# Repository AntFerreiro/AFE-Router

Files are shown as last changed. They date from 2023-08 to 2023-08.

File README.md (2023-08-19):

# AFE Router Documentation
This repository contain all materials for the assembly of the second version of this CNC Machine. 

This documentation is free and any commercial use is not allowed. Make sure to follow the repository to get the latest updates.

I hope you enjoy the project!

## Software
This machine is based on Marlin for the firmware. An extra branch has been created for this machine [AFE Router Version 2.0](https://github.com/AntFerreiro/Marlin)
For extra support and documentation for the firmware, go check the official [Marlin](https://github.com/MarlinFirmware/Marlin) repository.

## Drawings
Drawings are provided since not everyone may use the STL files as they are. Drawings make possible to modify some pieces so the still match with the rest of the machine.

## STL Files
STL files can be downloaded from this repository and can also be found in [Thingiverse](https://www.thingiverse.com/aferreiro_21/designs)
There is also the first version of this machine as well as some other designs I made.

## CNC Programs
You can also have a look at some of the CNC programms I use in the dayly work. This CNC programs are already tested in my machine but they may need some modifications if your machine is different (workspace limits for example).

## Bill of materials
The Hardware I used for this machine will be listed as well as the price I paid for them. This may vary with time depending on some temporary offers.

## Assembly instructions
There is no assembly manual that you can follow step by step. However here is the video I made when I built my machines. Since this is a progressive project. Not every step may be filmed in the video so make sure to subscribe to get the latest modifications.

Watch full video (https://www.youtube.com/watch?v=1IjvXwbKiRI)

## Do you want to support?
I'm not selling anything so if you want to support me, you can follow me on [social media](https://www.instagram.com/truewoodpecker/) and visit my [YouTube](https://www.youtube.com/@antonioferreiro) channel to give a big like and subscribe!

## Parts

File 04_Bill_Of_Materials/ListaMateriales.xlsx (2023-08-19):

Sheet: Hardware
 |  |  | Total Cost | 423.82
Item | Qty | Specs | Desctription | Price
Screw Bar | 3 | Pitch 2mm Lead 8mm, 100mm |  | 3.31 | https://es.aliexpress.com/item/1005004337655460.html
 | 1 | Pitch 2mm Lead 8mm, 600mm |  | 10.5
 | 2 | Pitch 2mm Lead 8mm, 400mm |  | 5.3
 | 1 | Pitch 2mm Lead 8mm, 250mm |  | 4
PowerSupply | 1 | 48V |  | 28.5 | https://es.aliexpress.com/item/1005002728038351.html
 | 1 | 12V |  | 8.21 | https://www.banggood.com/de/Geekcreit-AC-100-240V-to-DC-12V-5A-60W-Switching-Power-Supply-Module-Driver-Adapter-LED-Strip-Light-p-1441620.html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
Spindle | 1 | 400W | ER11 | 45.8 | https://es.aliexpress.com/item/32927775609.html
Nuts | 1 | M5 |  | 13.95 | https://es.aliexpress.com/item/32966882545.html
 | 1 | M3 |  | 15
Linear Bearing | 2 | MGN15H, 400mm |  | 22 | https://es.aliexpress.com/item/4000264234020.html
 | 2 | MGN15H, 600mm |  | 31.63
 | 2 | MGN9C |  | 7.32
 | 2 | MGN9C, 200mm |  | 11.31
Aluminium Profile | 2 | 2080, 400MM |  | 15.095 | https://es.aliexpress.com/item/1005002645411058.html
 | 2 | 2020, 500MM |  | 7.625
 | 2 | 2080, 500MM |  | 18.29
 | 1 | 2080, 600mm |  | 23.85 | https://es.aliexpress.com/item/1005004324352655.html
Pulley | 1 | 20-30T W6 B5 |  | 1.5 | https://es.aliexpress.com/item/1005005247772974.html
Ramps 1.6 | 1 | 1.6 |  | 5 | https://es.aliexpress.com/item/1005005074906263.html?curPageLogUid=tiiyxxNTx6R9
Stepper Drivers | 4 | A4988 |  | 0.86 | https://es.aliexpress.com/item/1005001621676770.html?curPageLogUid=2uASGiAAFuzh
Arduino Mega | 1 |  |  | 17 | https://es.aliexpress.com/item/32513419382.html?curPageLogUid=S8TSfbzLelJ8

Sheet: Screws
 | INCOMPLETO!
tornilleria |  | cantidad | metrica | mm | mm alt | coment
 | display | 4 | M3 | 10
 | Estop | 2 | M3 | 10
 | Motor eje Y | 8 | M5 | 12 | 10
 |  | 8 | M3 | 12 |  | \_/
 |  | 2 | M3 | 5
 | Guias Y | 20 | M3 | 10
 | Base | 20 | M5 | 10
 |  | 16 | M3 | 5 | 8 | \_/
 |  | 48 | M5 | 10
 | Lateral eje X | 8 | M3 | 15
 |  | 16 | M3 | 20
 |  | 8 | M3 | 26 | 30
 |  | 8 | M5 | 30
 |  | 4 | M3 | 32 | 35
 | Guias x | 30 | M3 | 10
 | Perfil L | 2 | M3 | 11 | 15
 | Guias Z | 18 | M3 | 10 | 12
 | soporte rodamiento | 2 | M4 | 75

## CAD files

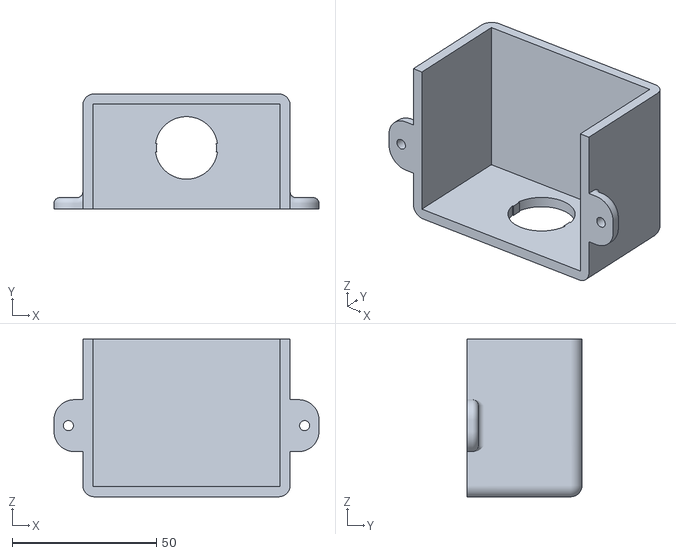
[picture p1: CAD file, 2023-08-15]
02_STL files/01_Base/EStop_Cover.stl
92.0 x 40.0 x 54.7

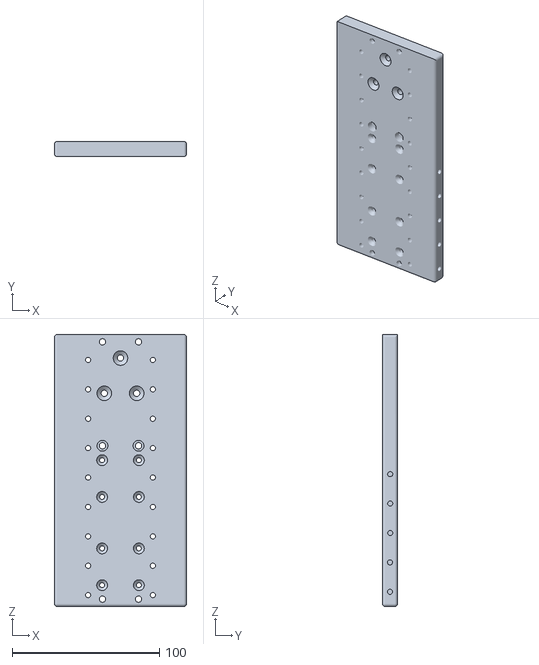
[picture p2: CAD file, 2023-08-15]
02_STL files/02_X_carriage/Carro_eje_X_plate.stl
90.0 x 10.3 x 185.0

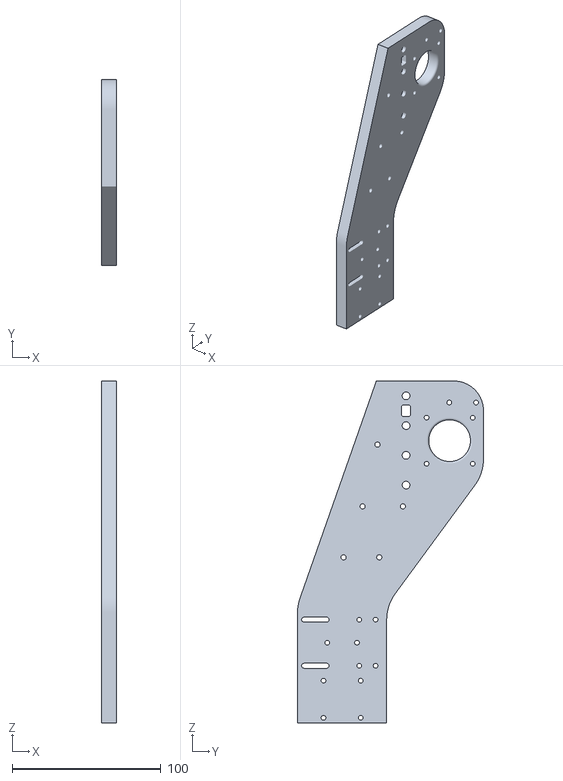
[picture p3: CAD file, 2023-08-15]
02_STL files/03_Y_carriage/Carro_eje_Y_plate_mot.stl
10.0 x 125.1 x 230.0

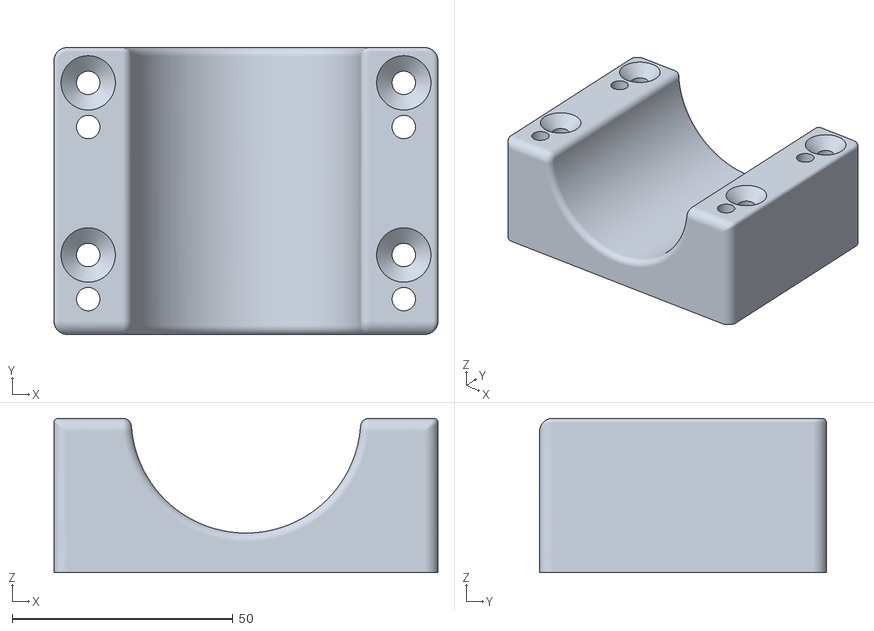
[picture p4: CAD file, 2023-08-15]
02_STL files/04_Z_carriage/spindle_holder_53mm.stl
87.0 x 65.0 x 35.0

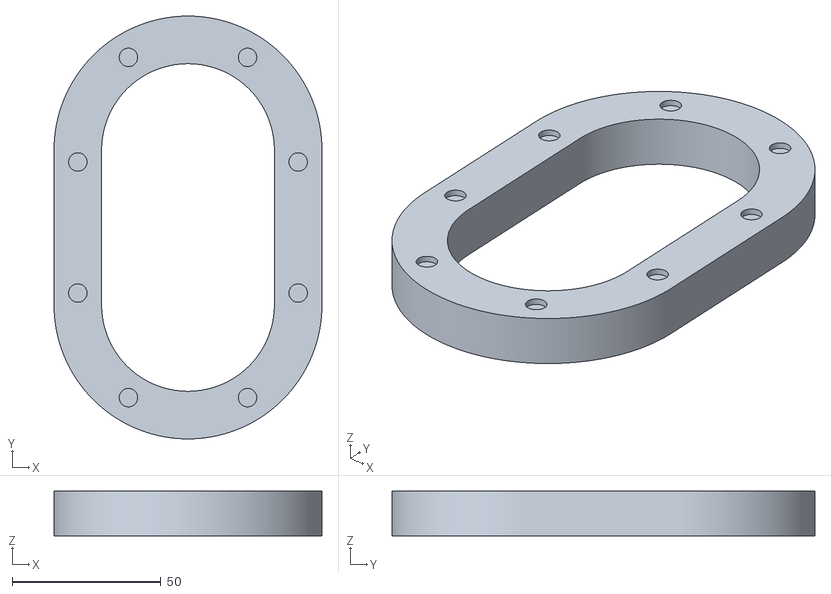
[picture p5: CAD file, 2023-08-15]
02_STL files/05_Vacuum/Foam_holder.stl
90.0 x 142.0 x 15.0

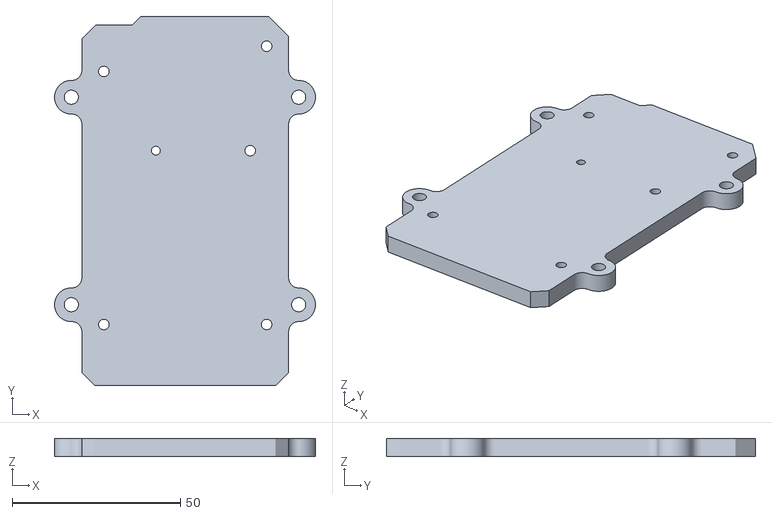
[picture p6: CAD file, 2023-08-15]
02_STL files/01_Base/ramps_1.6_holder.stl
77.5 x 109.6 x 5.45

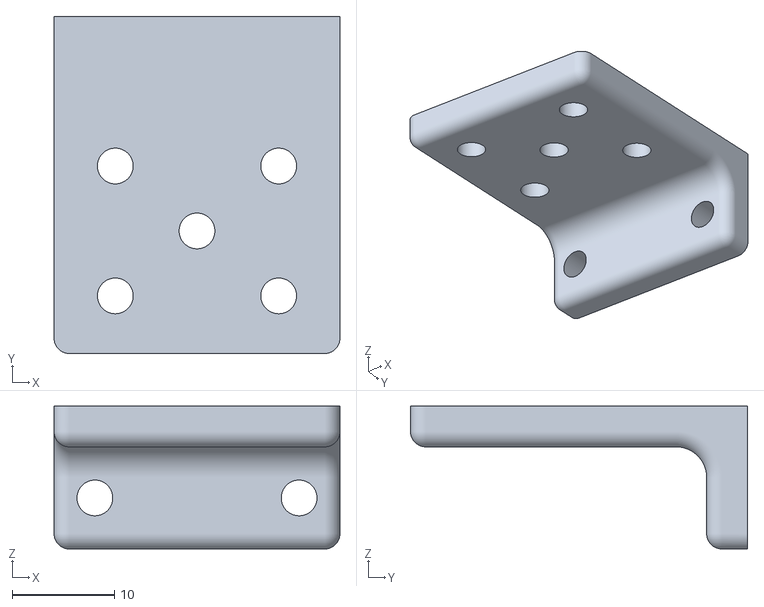
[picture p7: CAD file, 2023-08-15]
02_STL files/03_Y_carriage/CableChain_holder.stl
28.0 x 33.0 x 14.0

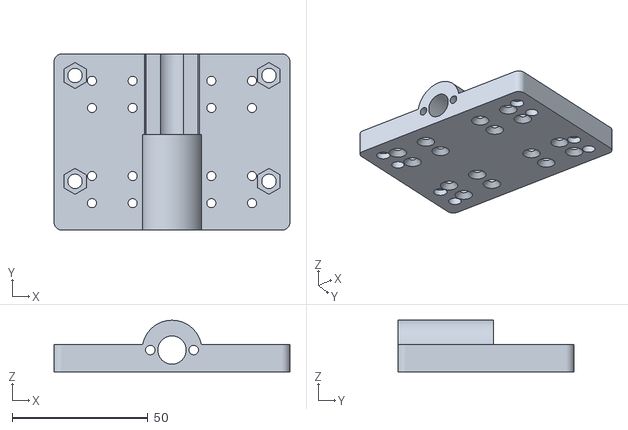
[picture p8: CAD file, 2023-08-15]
02_STL files/04_Z_carriage/Carro_eje_Z_platev2.stl
87.0 x 65.0 x 19.0

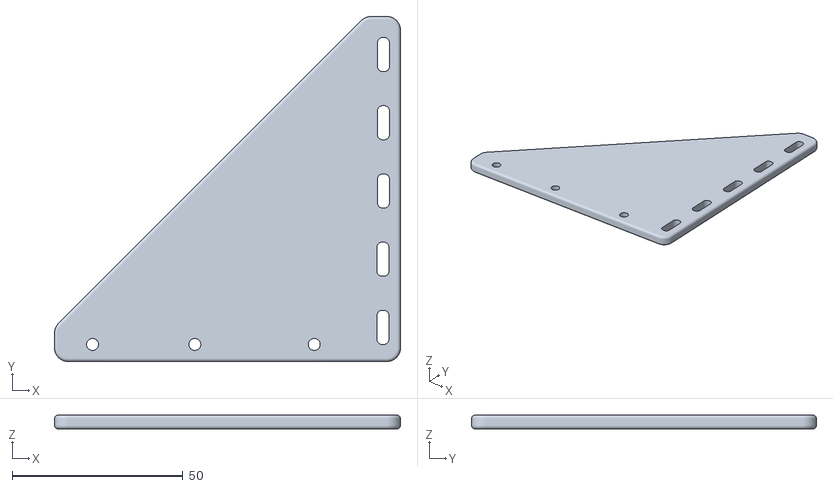
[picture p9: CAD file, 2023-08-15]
02_STL files/05_Vacuum/Vacuum_holder2.stl
101.5 x 101.2 x 4.00

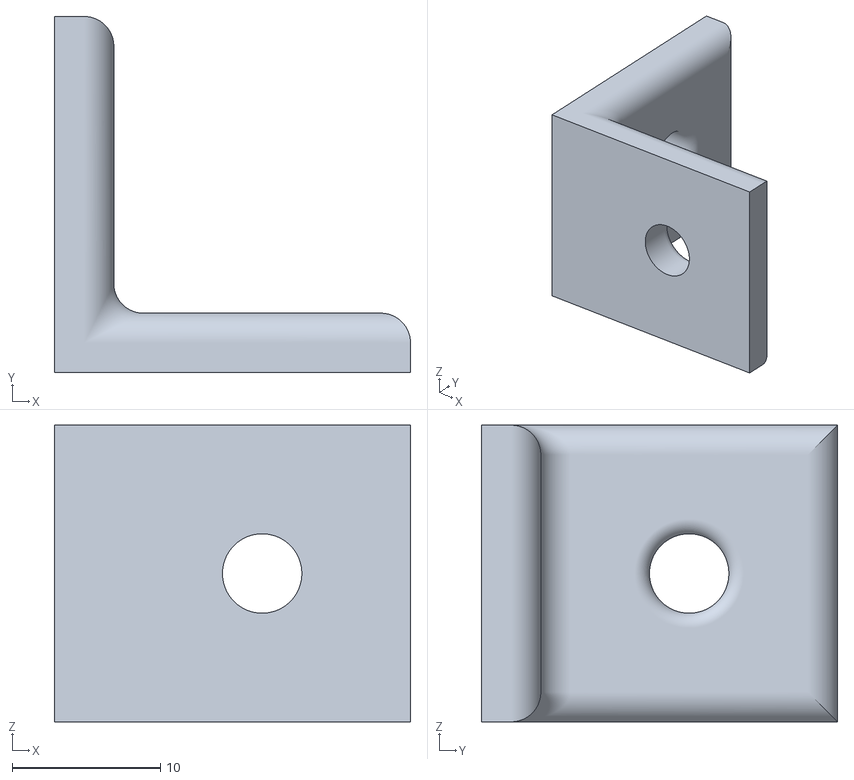
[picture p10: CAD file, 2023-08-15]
02_STL files/01_Base/Fixment.stl
24.0 x 24.0 x 20.0

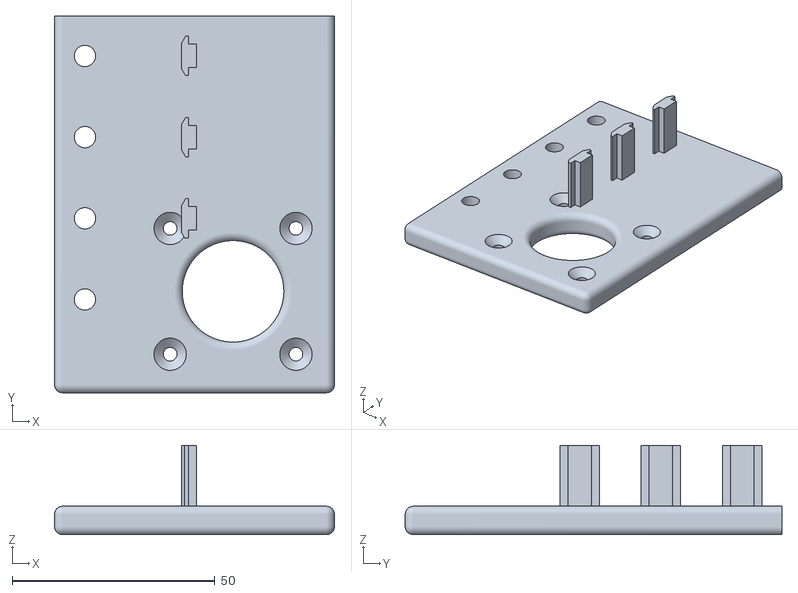
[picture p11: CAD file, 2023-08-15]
02_STL files/01_Base/Motor_Cover_2.stl
69.0 x 92.8 x 22.0

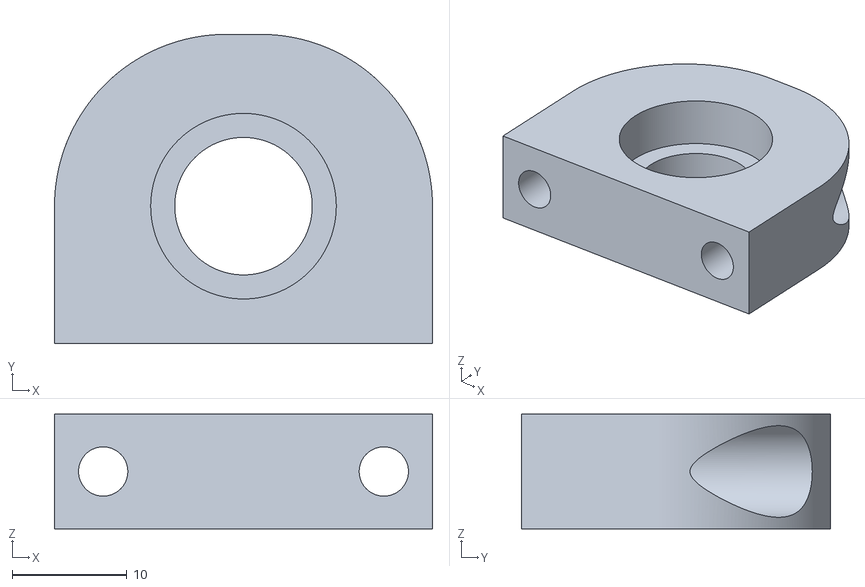
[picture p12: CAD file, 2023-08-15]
02_STL files/02_X_carriage/bearing_holder2_conic.stl
33.0 x 27.0 x 10.0

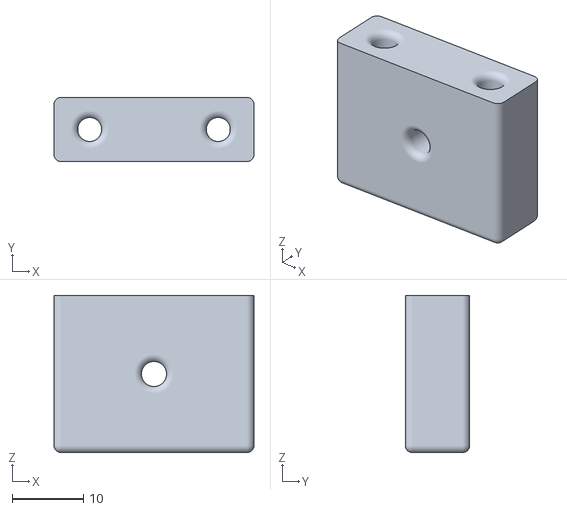
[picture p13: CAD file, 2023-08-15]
02_STL files/03_Y_carriage/Profile_holder.stl
28.0 x 9.00 x 22.0

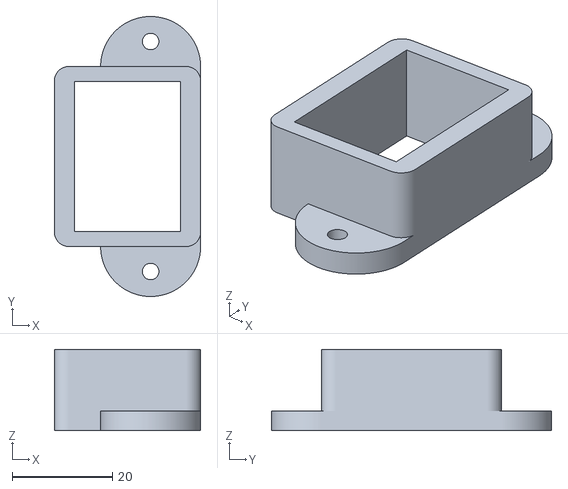
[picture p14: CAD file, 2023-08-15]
02_STL files/01_Base/Switch_holder.stl
29.2 x 56.0 x 16.3

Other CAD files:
02_STL files/02_X_carriage/Carro_eje_X_plate_back.stl
02_STL files/03_Y_carriage/Carro_eje_Y_plate.stl
02_STL files/01_Base/AC_DC_12V_support.stl
02_STL files/01_Base/Fan_Holder.stl
02_STL files/01_Base/AC_holder.stl
02_STL files/01_Base/Fixment20x20.stl
02_STL files/01_Base/Relay_holder.stl
02_STL files/01_Base/Top_Display.stl
02_STL files/01_Base/USB_holder.stl
02_STL files/01_Base/bearing_holder.stl
02_STL files/02_X_carriage/Carro_eje_X_plate_bottom.stl
02_STL files/02_X_carriage/Carro_eje_X_plate_top1.stl
02_STL files/02_X_carriage/LSHolder_v3.stl
02_STL files/02_X_carriage/LeadScrew_Block2.stl
02_STL files/02_X_carriage/LeadScrew_Block3.stl
02_STL files/02_X_carriage/bearing_holder2.stl
02_STL files/02_X_carriage/bearing_holder2Vscrew.stl
02_STL files/02_X_carriage/bearing_holder2_flat.stl
02_STL files/03_Y_carriage/LeadScrew_Block1.stl

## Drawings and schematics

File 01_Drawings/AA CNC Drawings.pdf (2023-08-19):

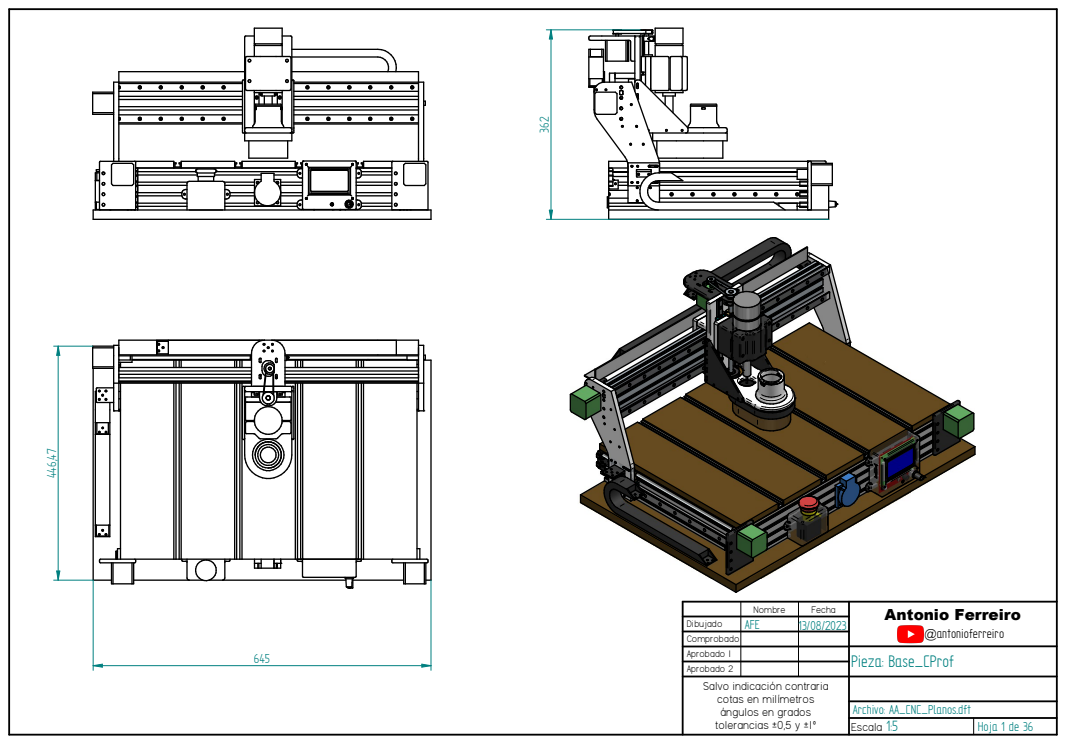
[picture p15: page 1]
Archivo: AA_CNC_Planos.dft

Nombre | Fecha | Antonio Ferreiro @antonioferreiro

Dibujado | AFE | 13/08/2023
Comprobado
Aprobado 1 | | | Pieza: Base_CProf
Aprobado 2
Salvo indicación contraria cotas en milímetros ángulos en grados tolerancias ±0,5 y ±1º

Escala 1:5 | Hoja 1 de 36

Nombre | Fecha | Antonio Ferreiro @antonioferreiro

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

Escala 1:5 | Hoja 2 de 36

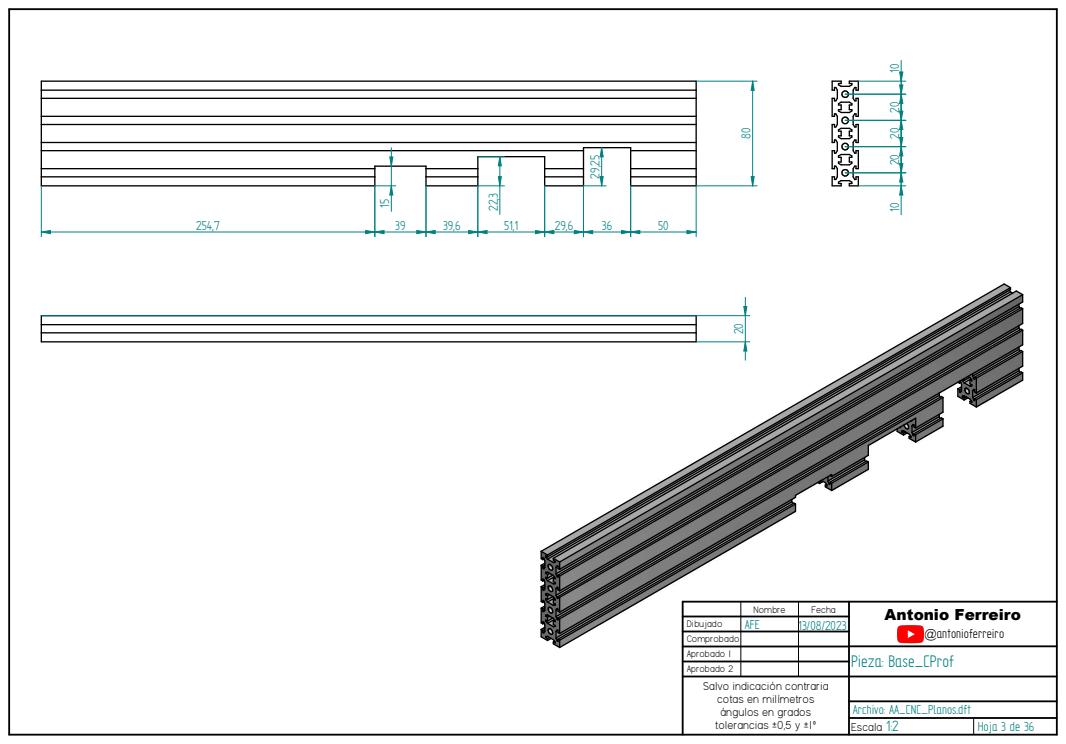
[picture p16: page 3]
Archivo: AA_CNC_Planos.dft

Nombre | Fecha | Antonio Ferreiro @antonioferreiro

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

Escala 1:2 | Hoja 3 de 36

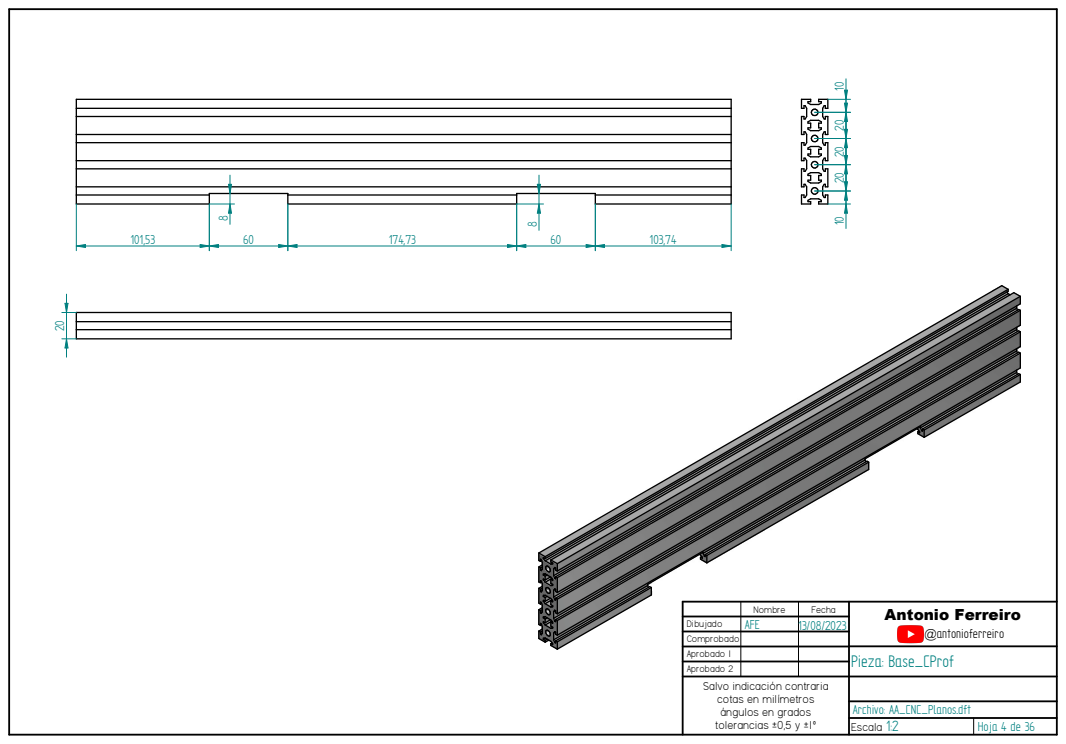
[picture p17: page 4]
Archivo: AA_CNC_Planos.dft

Nombre | Fecha | Antonio Ferreiro @antonioferreiro

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

Escala 1:2 | Hoja 4 de 36

Nombre | Fecha | Antonio Ferreiro @antonioferreiro

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

Escala 1:2 | Hoja 5 de 36

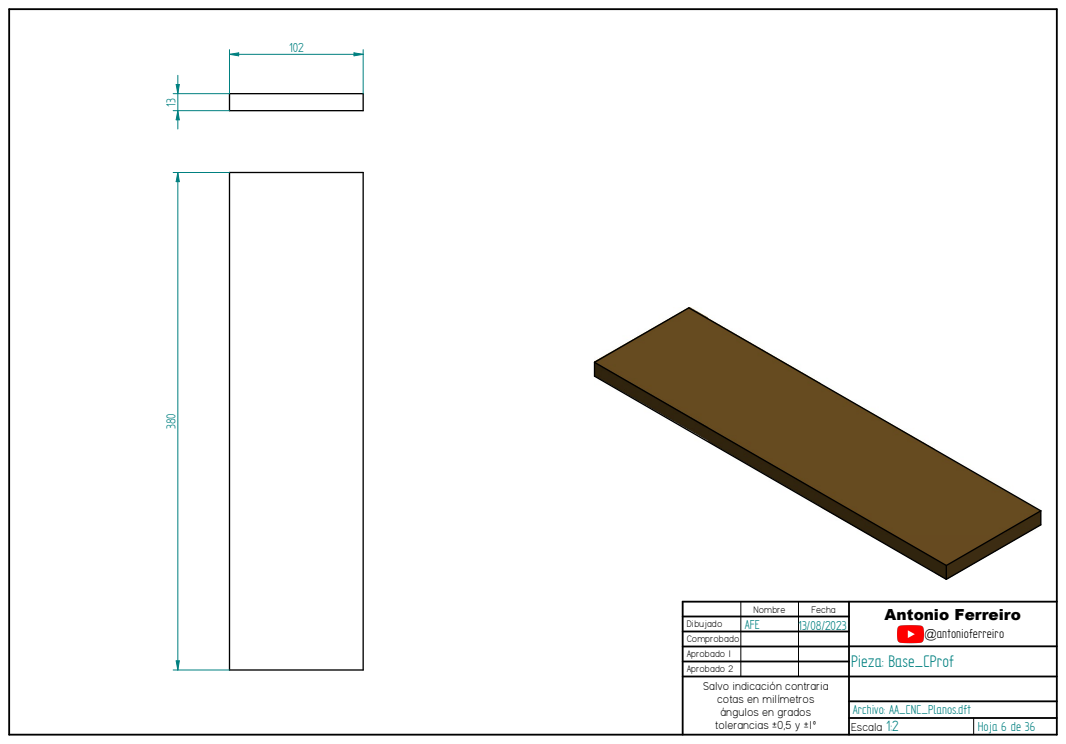
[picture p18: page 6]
Archivo: AA_CNC_Planos.dft

Nombre | Fecha | Antonio Ferreiro @antonioferreiro

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

Escala 1:2 | Hoja 6 de 36

# 5 5 ⁹ ⁶⁰ ²³,5

# 7,01 6,46 2¹,04 ¹¹,96 53

Nombre | Fecha | Antonio Ferreiro @antonioferreiro

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

Escala 1:1 | Hoja 7 de 36

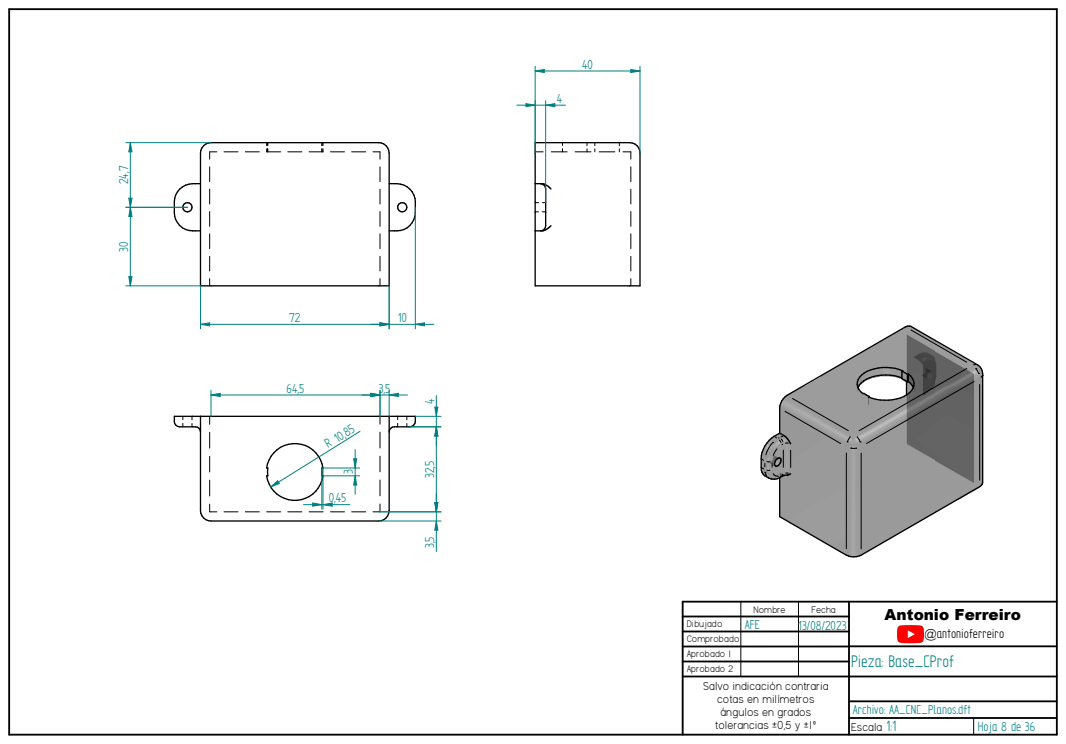
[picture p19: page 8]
Archivo: AA_CNC_Planos.dft

Nombre | Fecha | Antonio Ferreiro @antonioferreiro

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

Escala 1:1 | Hoja 8 de 36

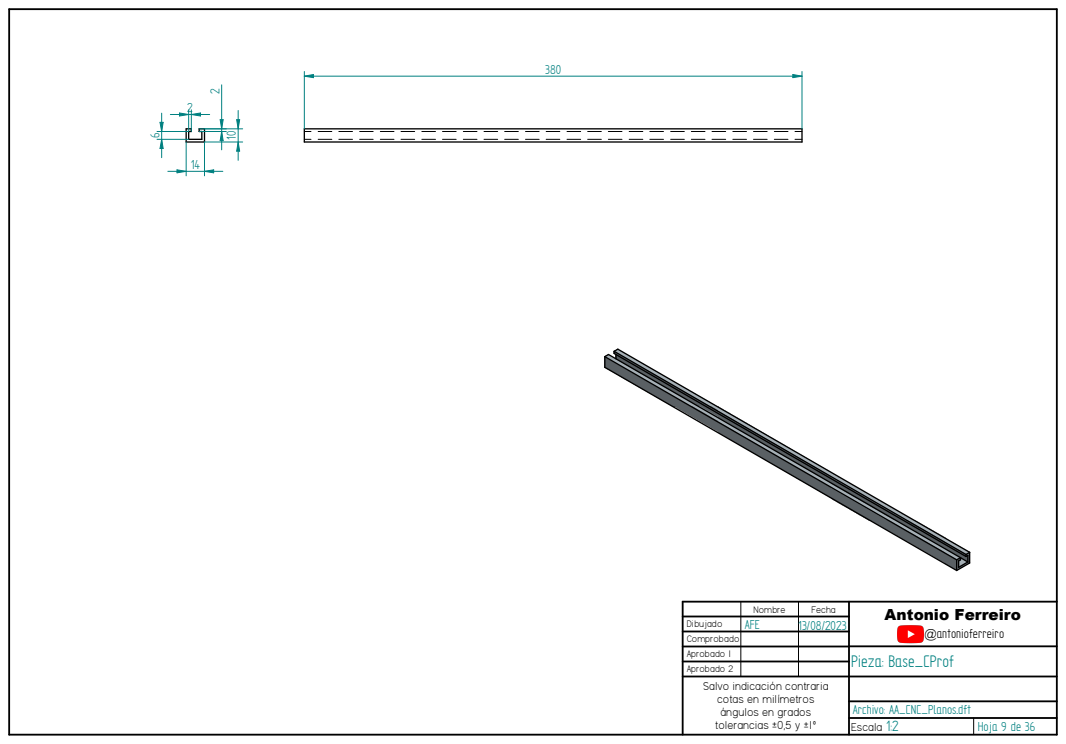
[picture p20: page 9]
Archivo: AA_CNC_Planos.dft

Nombre | Fecha | Antonio Ferreiro @antonioferreiro

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

Escala 1:2 | Hoja 9 de 36

Nombre | Fecha | Antonio Ferreiro @antonioferreiro

Dibujado | AFE | 13/08/2023
Comprobado
Aprobado 1 | | | Pieza: Base_MotorHolder
Aprobado 2
Salvo indicación contraria cotas en milímetros ángulos en grados tolerancias ±0,5 y ±1º

Escala 2:1 | Hoja 10 de 38

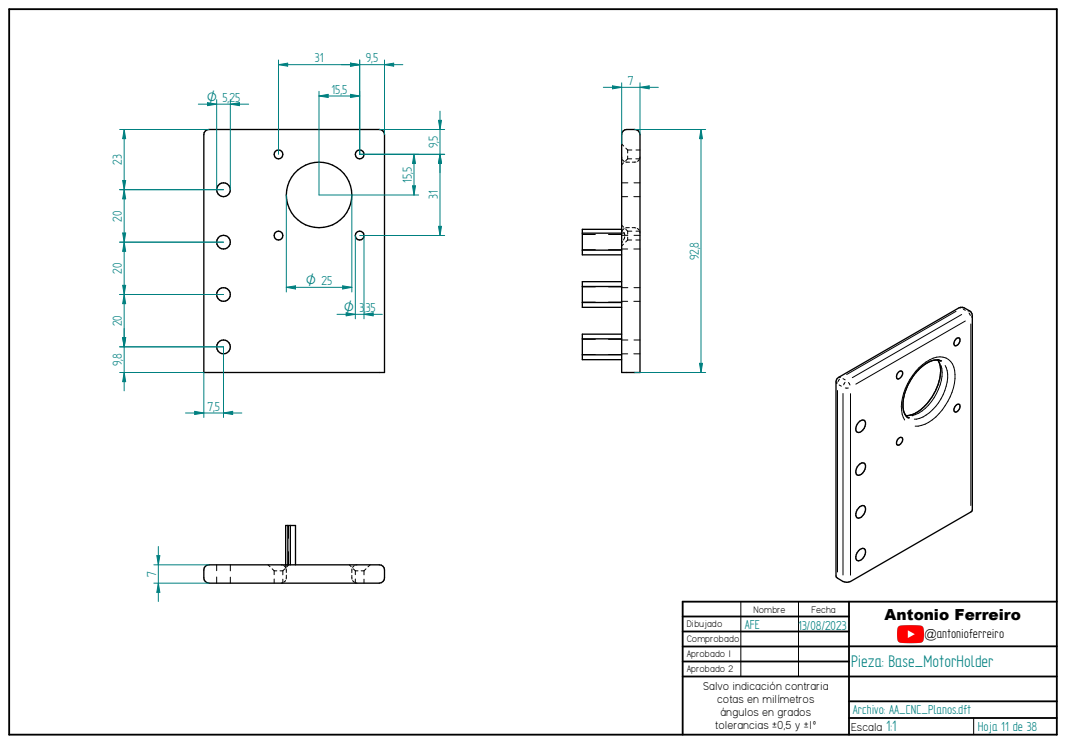
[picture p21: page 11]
Archivo: AA_CNC_Planos.dft

Nombre | Fecha | Antonio Ferreiro @antonioferreiro

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

Escala 1:1 | Hoja 11 de 38

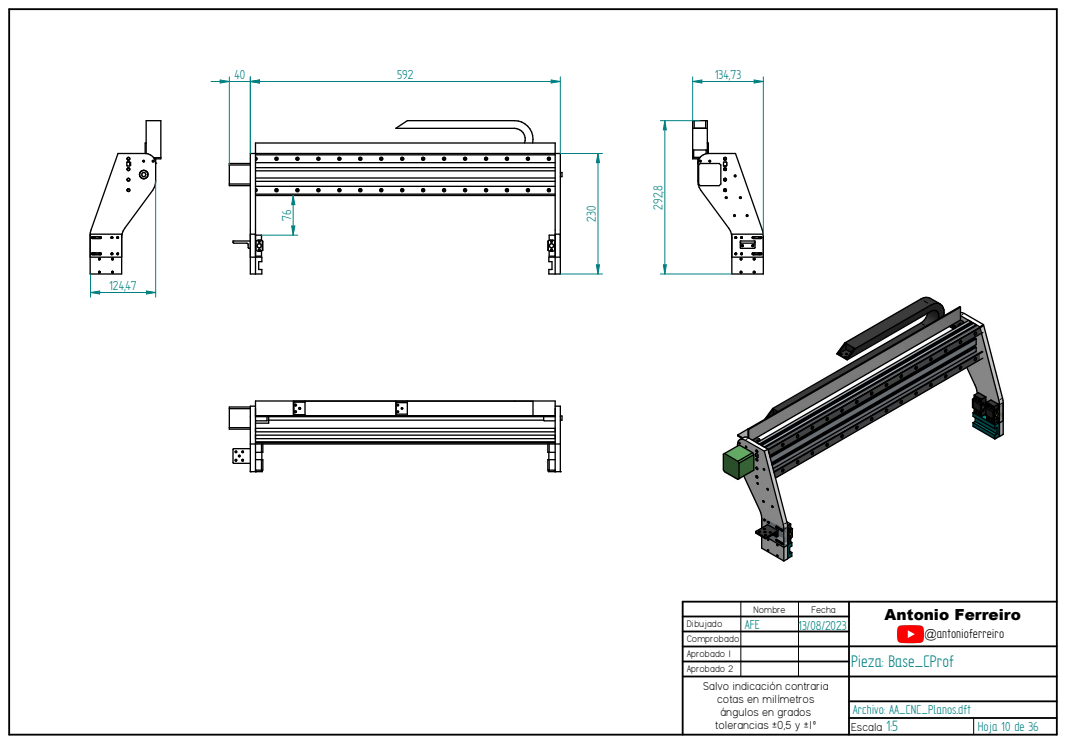
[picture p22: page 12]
Archivo: AA_CNC_Planos.dft

Nombre | Fecha | Antonio Ferreiro @antonioferreiro

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

Escala 1:5 | Hoja 10 de 36

Nombre | Fecha | Antonio Ferreiro @antonioferreiro

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

Escala 1:2 | Hoja 11 de 36

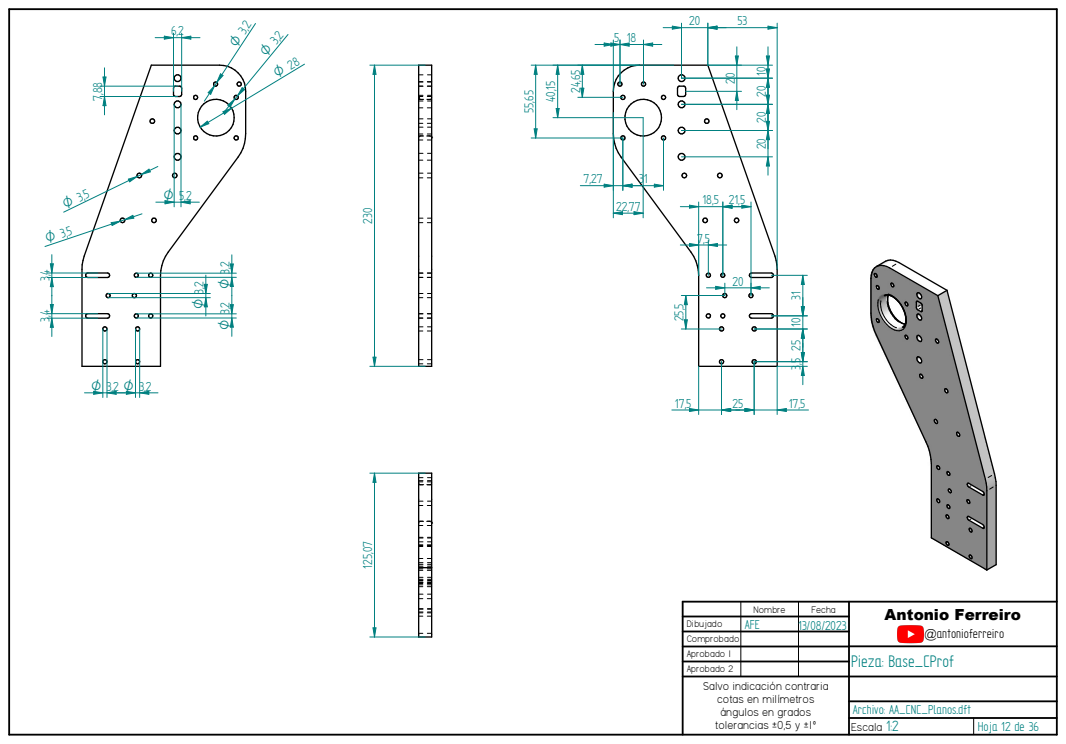
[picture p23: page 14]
Archivo: AA_CNC_Planos.dft

Nombre | Fecha | Antonio Ferreiro @antonioferreiro

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

Escala 1:2 | Hoja 12 de 36

Nombre | Fecha | Antonio Ferreiro @antonioferreiro

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

Escala 1:2 | Hoja 13 de 36

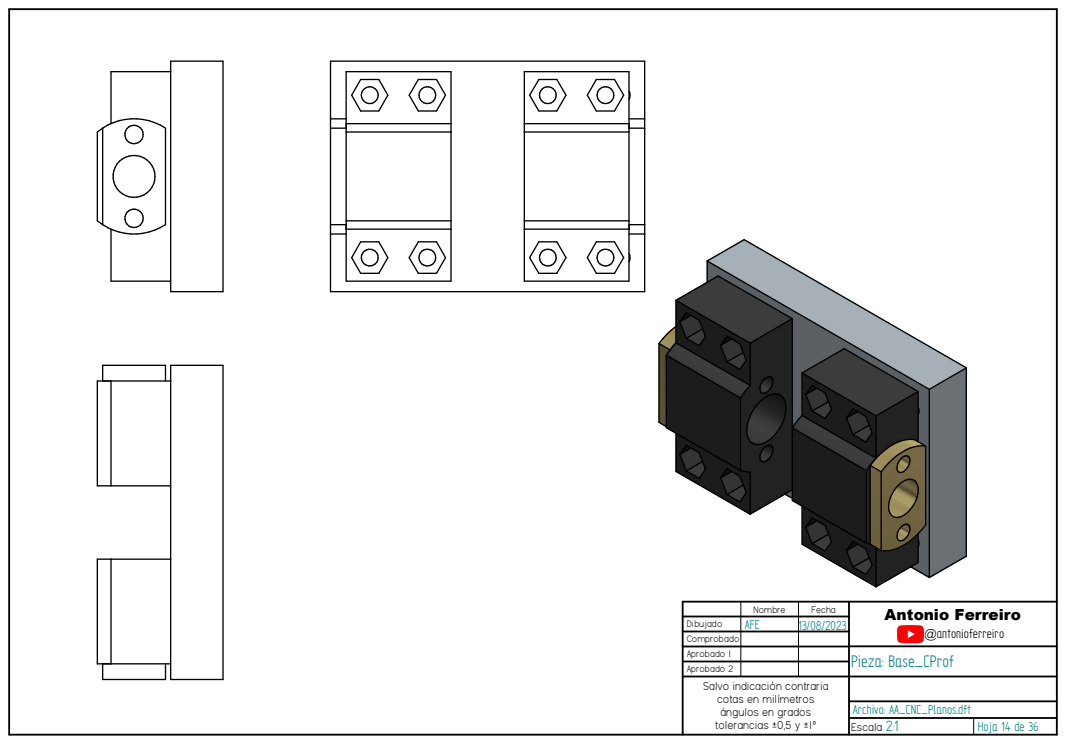
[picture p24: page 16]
Archivo: AA_CNC_Planos.dft

Nombre | Fecha | Antonio Ferreiro @antonioferreiro
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

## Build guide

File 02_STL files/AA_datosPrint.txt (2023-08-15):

Bearing holder 			(1 normal, 1 Mirror)	28Min
Motor_Cover_2			(1 normal, 1 Mirror)	1h48min		31g
LeadScrew_Block1		(4 normal)				32min		8g
spindle_holder_53mm		(1 normal)				5h4min		96gr
spindle_clip_53mm		(1 normal)				4h6min		78g
Motor_support			(1 normal)				2h47min		51gr
bearing_holder2			(2 normal)				20min		6gr
CableChain_holder		(1 normal)				25min		7gr
Profile_holder			(2 normal)				20			6gr		
Fixment					(28normal)				11min		4gr	
Fixment20x20			(10 normal)				9min		3			

---- Vacuum ----
Vacuum_holder1			(1 normal)				3h30min		68gr
Vacuum_holder2			(1 normal, 1 Mirror)	1h48min		19gr
Foam_holder				(1 normal)				3h33min		71gr
Hose_Holder				(1 normal)				1h23min		26gr	
Hose_Clip				(1 normal)				17min		6gr

---- Front pannel ----
Top_Display				(1 normal)				3h5min		63g
EStop_Cover				(1 normal)				2h10min		42gr

---- carro eje x ----
Carro_eje_X_plate		(1 normal)				6h7min		113gr
Carro_eje_X_plate_back	(1 normal)				2h37min		56gr
Carro_eje_X_plate_top1	(1 normal)				1h35min		27gr
Carro_eje_X_plate_bottom(1 normal)				1h33min		27gr
LeadScrew_Block2		(1 normal)				40min		10gr
LeadScrew_Block3		(1 normal)				20min		7gr

---- carro eje x ----
Carro_eje_Z_plate		(1 normal)				3h12min		67gr

---- carro eje y ----
Carro_eje_Y_plate		(1 normal)				5h16min		118gr
Carro_eje_Y_plate_mot	(1 normal)				5h51min		122gr

---- Back pannel ----
Switch_holder			(1 normal)				28min		10gr
AC_holder				(1 normal)				32min		9gr
USB_holder				(1 normal)				19min		5gr
Fan_Holder				(1 normal)				18min		5gr

---- Holders ----
DC_12V_support		(1 normal)				57min		20gr
Relay_holder			(1 normal)				58min		21gr
LSHolder_v2				(4 normal)				9min		3gr
LSHolder_v3				(1 normal)				14min		4gr

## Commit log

2023-08-15 AFE: STL files initial commit
    [AC_DC_12V_support.stl, AC_holder.stl, CableChain_holder.stl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]
2023-08-19 AFE: Bill of Materials
    [ListaMateriales.xlsx]
